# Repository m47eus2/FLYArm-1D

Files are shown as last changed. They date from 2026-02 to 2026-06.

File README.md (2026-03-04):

# FLYArm-1D

## Pendulum acting as a 1-DOF drone simulator

Embedded control system - custom 3D printed pendulum acting as 1-DOF drone simulator enabling stabilization at a desired angle. Simplified simulator of drone dynamics with one degree of freedom. 

The goal is to stabilize the pendulum at a desired angle using BLDC motor with a proppeler as actuator and feedback from MPU6050 IMU. 

The project combines embedded programming, control theory, sensor fusion and mechanical design.

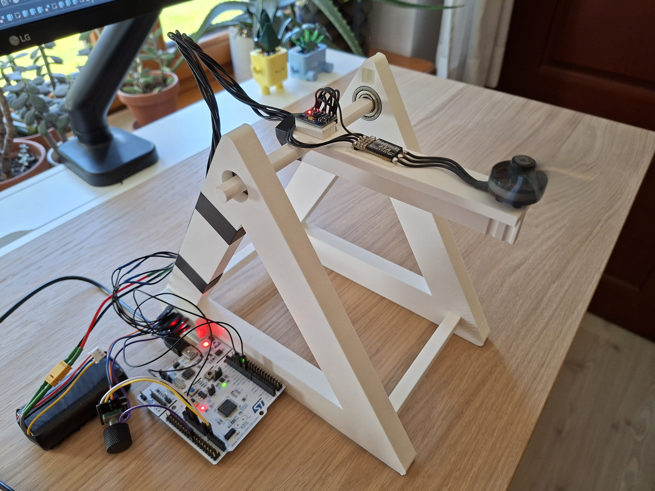
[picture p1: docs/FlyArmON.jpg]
FLYArm Running

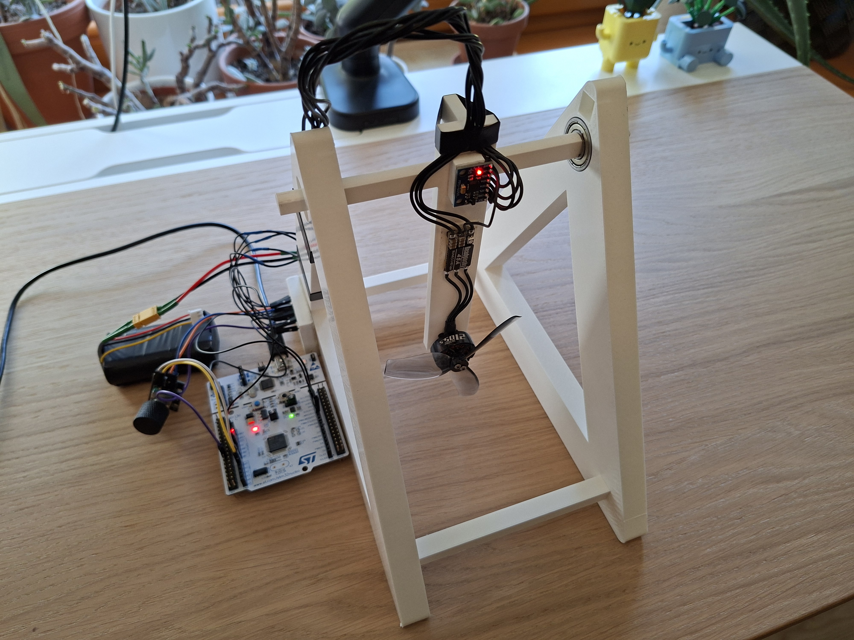
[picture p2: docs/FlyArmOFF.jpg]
FLYArm

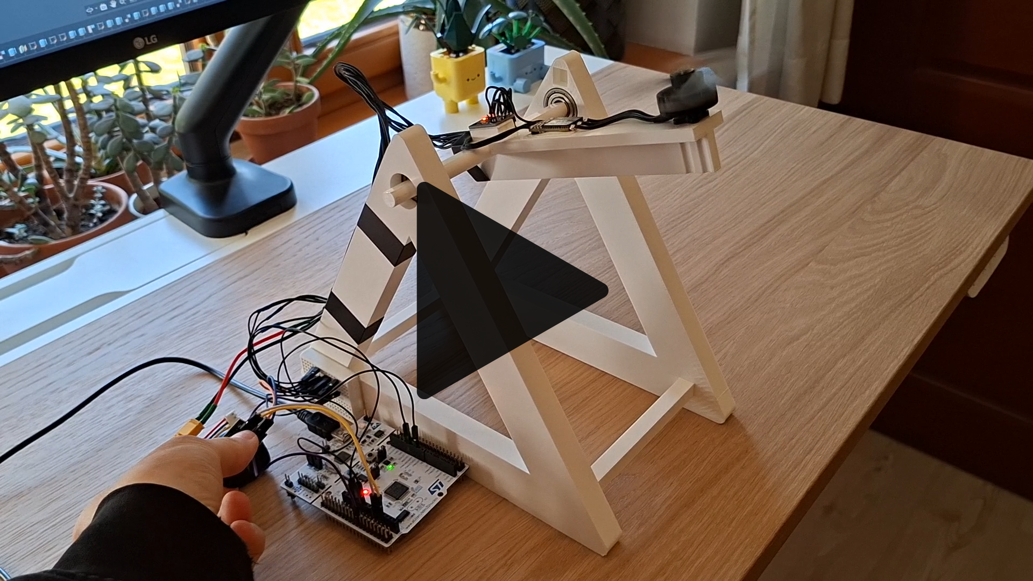
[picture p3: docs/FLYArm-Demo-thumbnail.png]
FlyArm Demo (https://youtu.be/Zwqv8pTMIBk)


## System Architecture
- MCU: STM32 Nucleo L476RG
- Actuator: BLDC motor with proppeler mounted at the end of the pendulum, driven by BlHeli_S ESC
- Feedback: MPU6050 IMU using complementary filter to combine gyro and accelerometer data
- Control algorithms: PID, LQR
- Power Supply: Li-ion 18650 2S high current pack

## Mechanical Design
- Custom pendulum structure designed and 3D printed
- Only not 3D printed part - metal bearings
- Designed in Autodesk Fusion
- 3D printed with PLA on Prusa i3MK3S+

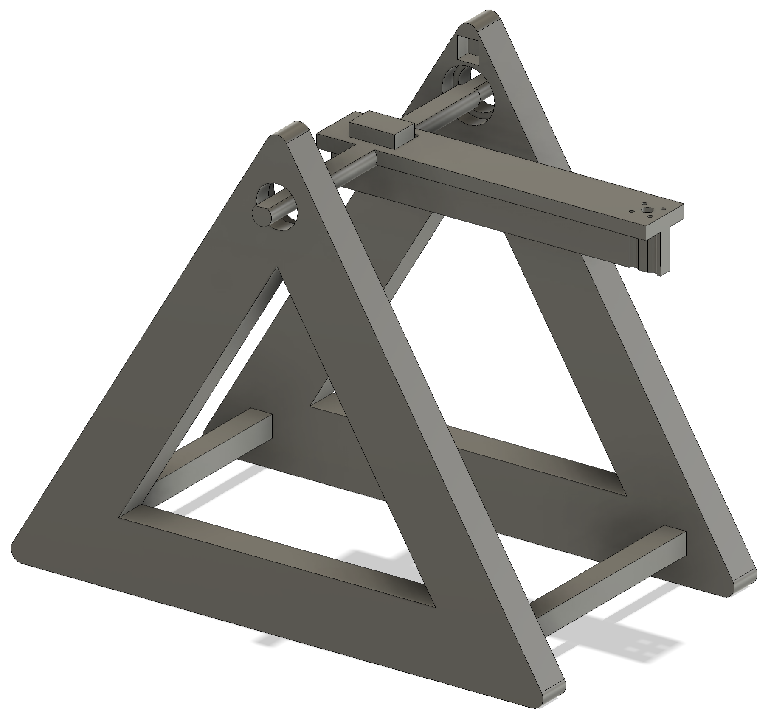
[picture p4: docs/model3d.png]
FLYArm 3D model


## Digital Twin
A digital twin of the system was developed for LQR regulator design.
Model was implemented in Python and validated by comparing simulated responses with measurments from the real system.

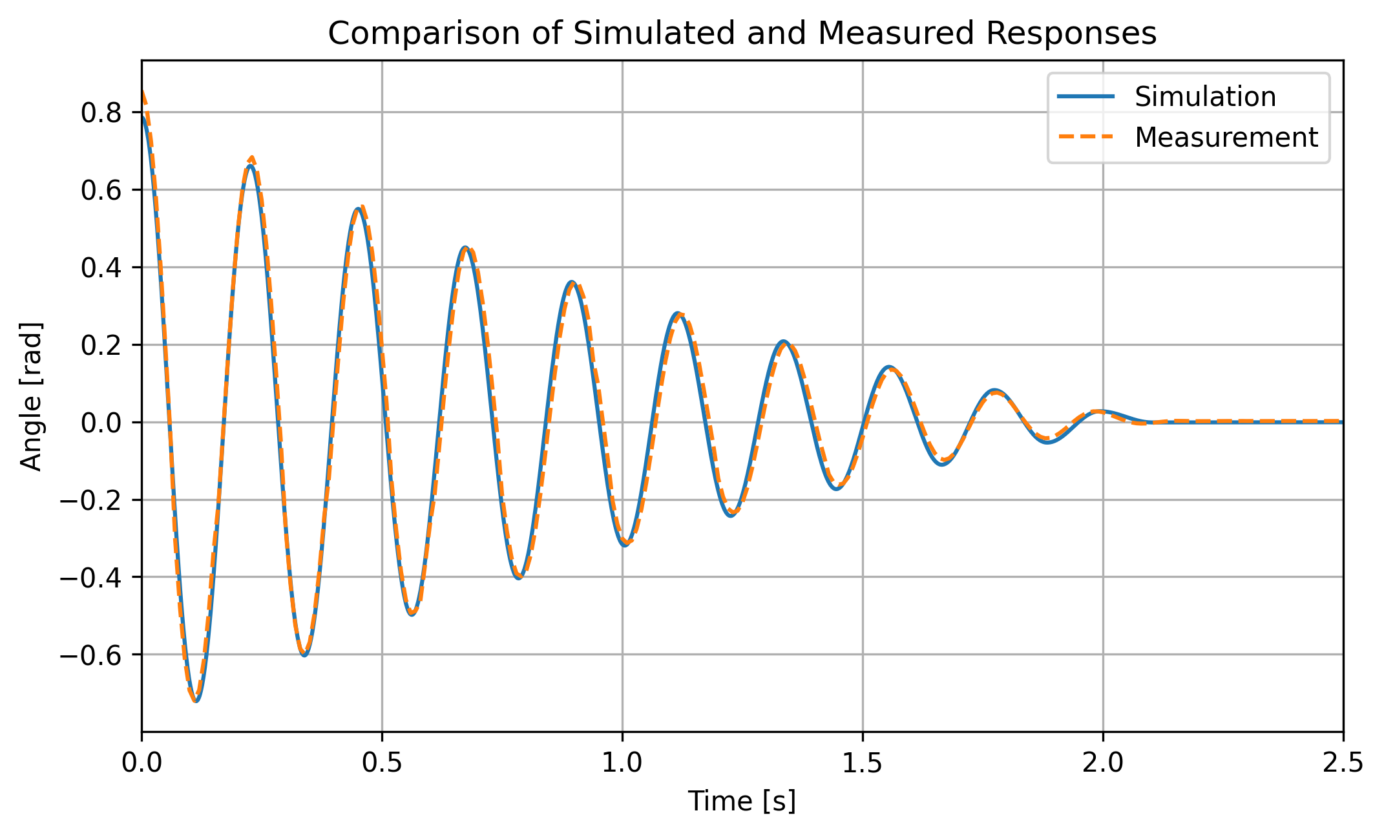
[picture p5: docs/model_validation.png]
Model Validation - Comparison of Simulated and Measured Responses


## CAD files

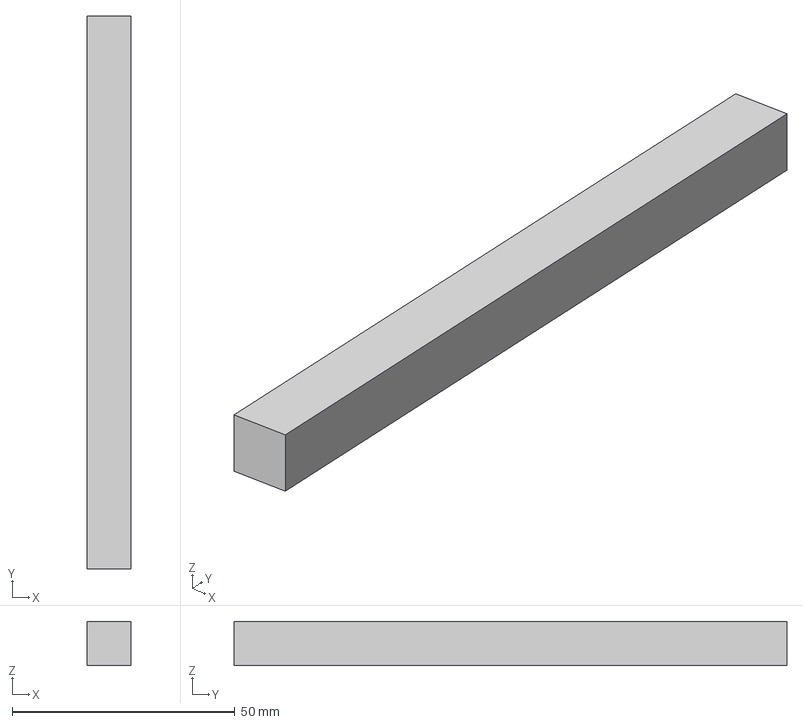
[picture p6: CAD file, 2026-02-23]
cad/Connector.3mf
9.90 x 124.0 x 9.90 mm

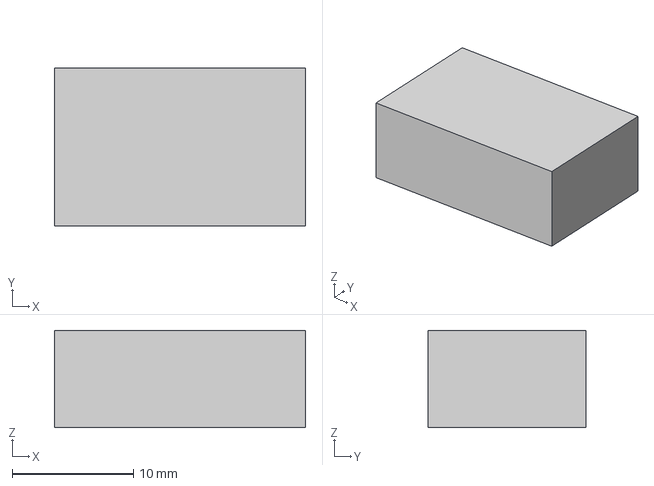
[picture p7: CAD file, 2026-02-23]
cad/MpuHolder.3mf
20.7 x 13.0 x 8.00 mm

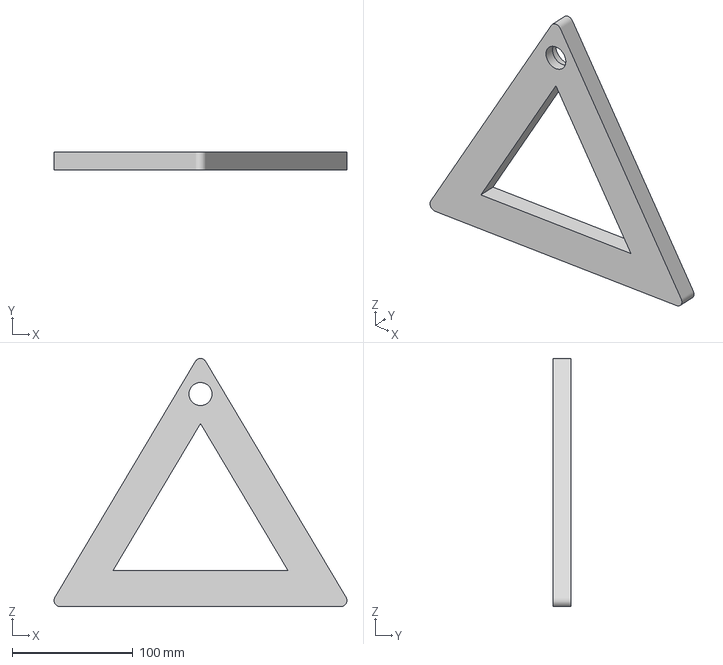
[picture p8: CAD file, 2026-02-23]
cad/BaseRight.3mf
242.4 x 15.0 x 205.2 mm

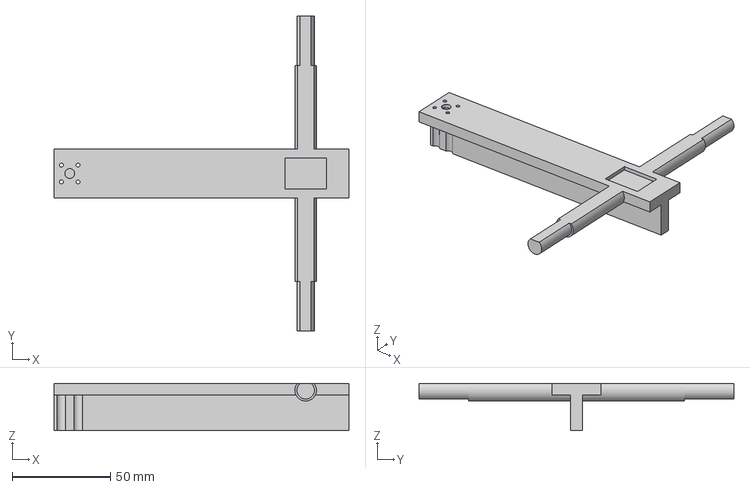
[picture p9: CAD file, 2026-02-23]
cad/Bar.3mf
150.0 x 160.0 x 24.0 mm

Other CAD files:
cad/FLYArm-1D.f3d

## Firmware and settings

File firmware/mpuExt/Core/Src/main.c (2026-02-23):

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
/* Includes ------------------------------------------------------------------*/
#include "main.h"
#include "i2c.h"
#include "tim.h"
#include "usart.h"
#include "gpio.h"

/* USER CODE BEGIN Includes */

#include <stdio.h>
#include "mpu6050.h"

/* USER CODE END Includes */


void SystemClock_Config(void);
/* USER CODE BEGIN 0 */

#define DT 0.01f

float accel[3], gyro[3], roll[3];
float dGyro, angle;
int16_t accelBias[3], gyroBias[3];
volatile uint8_t dataReady = 0;
int16_t encoderValue;
int16_t pwmValue, throttle, lqrOutput;
uint8_t estop = 0;
float eAccum = 0;

int __io_putchar(int ch){
	if(ch=='\n'){
		__io_putchar('\r');
	}
	HAL_UART_Transmit(&huart2, (uint8_t*)&ch, 1, HAL_MAX_DELAY);
	return 1;
}

int16_t control(float setAngle){
	float Kp = 5.0f;
	float Ki = 15.0f;
	float Kd = 0.5f;

	float e = setAngle - angle;
	eAccum = eAccum + e * DT;

	//Anty-windup
	if(eAccum > 22.0f){eAccum = 22.0f;}
	if(eAccum < 0.0f){eAccum = 0.0f;}
	if (estop == 1){eAccum = 0.0f;}
	if (encoderValue == 0){eAccum = 0.0f;}

	float P = Kp * e;
	float I = Ki * eAccum;
	float D = -1 * Kd * dGyro;

	float u = P+I+D;
	return (int16_t)u;
}

int16_t lqr(){
	float k1 = 31.6227766;
	float k2 = 31.36357997;
	float u1 = -k1 * ((angle * 0.01745329f) - 1.570796f);
	float u2 = -k2 * (dGyro * 0.01745329f);
	float u = u1 + u2 + 238.0f;
	return (int16_t)u;
}

void HAL_TIM_PeriodElapsedCallback(TIM_HandleTypeDef *htim){
	if(htim == &htim6){
		//
		// Readig data from MPU6050
		//

		mpu6050_ReadRoll(roll, &dGyro, accel, gyro);
		angle = roll[2]+90.f;
		//mpu6050_ReadRawBias(accelBias, gyroBias); // For reading biases

		//
		// Reading encoder value
		//

		encoderValue = __HAL_TIM_GET_COUNTER(&htim2);
		if(encoderValue < 0){encoderValue = 0;}
		if(encoderValue > 1000){encoderValue = 1000;}

		//
		// Safety stop
		//

		// Estop reset
		if((HAL_GPIO_ReadPin(button_GPIO_Port, button_Pin) == GPIO_PIN_RESET) && encoderValue == 0 && angle < 30){estop=0;}

		// Estop
		if(angle > 170.0f){estop=1;}

		//
		// Regulators - choose PID or LQR
		//

		if(encoderValue > 170){encoderValue = 170;}
		float setAngle = (float)encoderValue;

		// PID

		pwmValue = 160 + control(setAngle);

		// LQR

		//pwmValue = 160 + lqr();
		//lqrOutput = pwmValue;

		//
		// Motor manual controll
		//

		//pwmValue = 160 + encoderValue; - for manual motor control

		//
		// BLDC Motor controll
		//

		if(pwmValue < 160){pwmValue = 160;}
		if(pwmValue > 500){pwmValue = 500;}

		if((estop == 0) && encoderValue > 0){throttle = 1000+pwmValue;}
		else{throttle = 1000;}

		__HAL_TIM_SET_COMPARE(&htim3, TIM_CHANNEL_1, throttle);

		//
		// Setting flag to main (for sending data via UART)
		//

		dataReady = 1;
	}
}

/* USER CODE END 0 */

/**
  * @brief  The application entry point.
  * @retval int
  */
int main(void)
{

  /* MCU Configuration--------------------------------------------------------*/

  /* Reset of all peripherals, Initializes the Flash interface and the Systick. */
  HAL_Init();

  /* Configure the system clock */
  SystemClock_Config();

  /* Initialize all configured peripherals */
  MX_GPIO_Init();
  MX_I2C1_Init();
  MX_USART2_UART_Init();
  MX_TIM6_Init();
  MX_TIM2_Init();
  MX_TIM3_Init();
  /* Infinite loop */
  /* USER CODE BEGIN WHILE */

  // Encoder Init
  HAL_TIM_Encoder_Start(&htim2, TIM_CHANNEL_ALL);

  // PWM Output Init
  HAL_TIM_Base_Start_IT(&htim3);
  HAL_TIM_PWM_Start(&htim3, TIM_CHANNEL_1);
  __HAL_TIM_SET_COMPARE(&htim3, TIM_CHANNEL_1, 1000);

  // MPU6050 Init
  HAL_Delay(1000);
  mpu6050_Init();
  HAL_Delay(1000);

  // Callback Timer
  HAL_TIM_Base_Start_IT(&htim6);

  // Setting Ready LED
  HAL_GPIO_WritePin(led2_GPIO_Port, led2_Pin, GPIO_PIN_SET);

  while (1)
  {
	//
	// Telemetry via UART
	//
	if(dataReady==1){
		printf(">GyroX:%f\n", gyro[0]);
		printf(">GyroY:%f\n", gyro[1]);
		printf(">GyroZ:%f\n", gyro[2]);

		printf(">AccelX:%f\n", accel[0]);
		printf(">AccelY:%f\n", accel[1]);
		printf(">AccelZ:%f\n", accel[2]);

		printf(">RollAcc:%f\n", roll[0]);
		printf(">RollGyro:%f\n", roll[1]);
		printf(">RollFused:%f\n", roll[2]);

		printf(">Angle:%f\n", angle);
		printf(">Encoder:%d\n", encoderValue);
		printf(">Estop:%d\n", estop);
		printf(">Pwm:%d\n", pwmValue);
		printf(">throttle:%d\n", throttle);
		printf(">eAccum:%f\n", eAccum);
		printf(">lqrOutput:%d\n", lqrOutput);

		dataReady = 0;
	}
    /* USER CODE END WHILE */

    /* USER CODE BEGIN 3 */
  }
  /* USER CODE END 3 */
}

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


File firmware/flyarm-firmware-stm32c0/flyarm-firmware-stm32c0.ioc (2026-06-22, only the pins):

Mcu.UserName=STM32C031C6Tx
PA0.Signal=S_TIM1_CH1
PA13.Signal=DEBUG_SWDIO
PA14-BOOT0.Signal=DEBUG_SWCLK
PA2.Signal=USART2_TX
PA3.Signal=USART2_RX
PA5.GPIO_Label=userLed
PA5.Signal=GPIO_Output
PA6.Signal=S_TIM3_CH1
PA7.Signal=S_TIM3_CH2
PB8.Signal=I2C1_SCL
PB9.Signal=I2C1_SDA
PC13.GPIO_Label=userButton
PC13.Signal=GPIO_Input

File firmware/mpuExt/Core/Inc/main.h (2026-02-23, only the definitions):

#define button_Pin GPIO_PIN_13
#define button_GPIO_Port GPIOC
#define led2_Pin GPIO_PIN_5
#define led2_GPIO_Port GPIOA

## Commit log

2026-02-23 Adding STM32CubeIDE project
2026-02-23 Adding CAD files
    [Bar.3mf, BaseRight.3mf, Connector.3mf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]
2026-04-20 Port firmware to STM32C031C6T6
2026-06-22 stm32c0 firmware - Add encoder filter and delay before mpu6050 init

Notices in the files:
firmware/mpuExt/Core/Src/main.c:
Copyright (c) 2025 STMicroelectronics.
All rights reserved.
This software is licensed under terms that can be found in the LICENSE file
